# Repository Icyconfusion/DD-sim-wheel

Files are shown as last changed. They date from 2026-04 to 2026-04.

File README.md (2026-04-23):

# DD-sim-wheel
A Direct Drive (DD) wheel for simracing using a hoverboard motor and CAN bus.

I designed this wheel for simracing, to compete with high end direct drive wheels that offer great quality force feedback, except with a much lower price. The wheel has the capability to connect wheel rims, pedals, shifters, handbrakes etc and send those inputs, along with steering position to the PC as game inputs. In creating this project, I learned a lot about motor control and half bridge drivers.


# Assembly

The project can be separated into two parts, the wheelbase and the wheel rim.

For the wheelbase, the assembly consists of four horizontal 2020 profiles, allowing for mounting to rigs etc, and providing the basic structure of the base. Two vertical posts are attached by 90 degree connectors to enable mounting the cross beam for the motor.





The crossbeam (2040 profile) is important as it is the base structure for supporting and holding the motor in place. A thin steel plate (necessary to prevent damage and subsequent twisting of the the crossbeam as a result of the motor axle) is attached to the profile, with the flat part of the motor axle being locked on with the 3d printed clamp. This is the mechanism for holding the motor in place and preventing rotation in the axle. 





To prepare the motor, it is first necessary to disassemble it. First remove the tire as this wont be needed. Then remove the motor bell as we will need to drill holes into it. We will also need to drill into the axle. a 6x70mm bolt pattern is drilled in to the bell face, as well as a 30mm hole in the centre. This allows the mounting of the encoder and routing of wires. Drill a hole in the closed end of the axle, so that wires can run through.



The MT6701 encoder is attached to its mount, then press fit into the bearing on the bell side of the motor.





The diametric magnet for the encoder is glued into the hole on the inside of the magnet mount, this will be attached to the motor along with the quick release using the 6x70mm drilled holes.







The side covers attach to the four horizontal profiles using T nuts, and the PSU is mounted to the side cover using the mounting threads in the psu. The PCB is attached to its mount using the mounting holes, then attached to the vertical profile.











The USB C connectors are screwed onto the back plate, and power cables run through the two holes. The back, top and bottom plates/covers are mounted using T nuts.





The front plate is screwed directly into the tapped ends of the profiles. This is the wheelbase assembly.







For the wheel rim assembly, is is as simple as mounting the 12mm buttons using the nuts included, running the cable from the mcu into the USB c connector in the quick release, and then mounting the wheel rim, buttons box/plates and quick release using screws, and then pushing onto wheelbase.









# Electronics

### Schematic


I made my own 3 phase motor driver to handle the control of the hoverboard motor:


It uses an INA240 for current sensing for torque control, and an IR2104 IC so that the STM32 can control the MOSFETS.



Screw terminals to external connections:


And brake resistor circuit:


### PCB



It has M6 mounting holes for the wheelbase PCB mount. The PCB is organised with the motor driver at the top, and low voltage components below the STM32, which is connected by headers. It uses TO-220 mosfets, and 7.62mm screw terminals. The screw terminals on the bottom are to CAN connections, encoder and 5v power.



# Firmware

The wheelbase uses a modified version of OpenFFBoard firmware. OpenFFboard controls the motor including torque, responding to output from the PC/game to provide force feedback. I added my own CAN firmware into this to recieve CAN messages as inputs, and send them to the PC. This included writing my own CAN callback into the firmware.
For the wheel rim MCU, I wrote my own firmware for reading button inputs, and then sending via CAN bus. The MCU will only send a message when their is a change in button states e.g a press or release, this is to reduce interruption to the motor control firmware. The can message is as follows: if button one is pressed, then 00000001, which is 1x01. Or if buttons 1 and 4 are pressed, 00001001, 0x09.

# BOM

### Parts
| Name | Purpose |  Quantity  | Total cost (USD) | Link | Distributor |
|---|---|----|---|---|---|
| 10 ohm resistor | Resistor for the PCB | 5  | 1.32  | https://www.aliexpress.com/item/1005001437016232.html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 | Aliexpress |
| 90 degree brackets | mounting and assembling T slot profiles | 8  | 0.73  | https://jlcmc.com/product/s/T02/TPDB/die-cast-corner-bracket-eu-20-series-connector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 | JLCMC |
| T nuts | Mounting components to T slot profiles | 60 | 7.23  | https://www.aliexpress.com/item/1005007825040716.html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 | Aliexpress |
| Screws | M5 screws for assembling components. 10 of 16mm, 20 of 14mm, 4 of 30mm, 6 of 45mm, 6 of 65mm, 16 of 8mm. Also 10 of M2x14mm. | 76 | 1.79  | https://jlcmc.com/product/s/E02/EDLA/hex-socket-screw-full-partial-thread-standard-type-(din-912-gb-t-70.1) | JLCMC |
| IR2104 | IC for powering each phases mosfet | 3  | 2.28  | https://www.aliexpress.com/item/1005005970327760.html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 | Aliexpress |
| Small Cap | 0.47 uF 50V CAP | 10 | 5.03  | https://www.aliexpress.com/item/1005009938373275.html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 | Aliexpress |
| LM2596 | Buck converter for supplying low voltage power to the PCB | 1  | 2.56  | https://www.aliexpress.com/item/1005010036505161.html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 | Aliexpress |
| INA240 | The current amplifier to sense motor current with the shunt | 3  | 11.48 | https://www.aliexpress.com/item/1005007050377087.html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 | Aliexpress |
| MOSFET | IRF2204 mosfet for the 3 phase motor driver | 3  | 5.63  | https://www.aliexpress.com/item/1005008398718849.html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 | Aliexpress |
| Large Cap | 50V 2200uF capacitor for smoothing across power lines | 1  | 12.76 | https://www.aliexpress.com/item/1005005380342459.html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 | Aliexpress |
| MT6701 | The MT6701 is the encoder to track the position of the wheel rim. | 1  | 3.27  | https://www.aliexpress.com/item/1005010143099990.html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 | Aliexpress |
| STM32 | STM32 is the wheelbase PCB MCU. It runs the FFB firmware. | 1  | 10.62 | https://www.aliexpress.com/item/1005009620785965.html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 | Aliexpress |
| TVS diode | P6KE36A TVS diode for power on the PCB | 1  | 2.66  | https://www.aliexpress.com/item/1005008668996384.html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 | Aliexpress |
| RP2350 | RP2350 CAN is the devboard for the wheel rim. It has CAN included. | 1  | 16.93 | https://www.aliexpress.com/item/1005008827015596.html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 | Aliexpress |
| CAN resistor | 120 ohm termination resistor for CAN bus. | 2  | 1.35  | https://www.aliexpress.com/item/1005006730653425.html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 | Aliexpress |
| Shunt resistor | Constantan wire resistor for motor current sensing. 10mr 1.5x20 | 3  | 1.63  | https://www.aliexpress.com/item/1005003122854809.html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 | Aliexpress |
| Push Buttons | The pushbuttons are used for the steering rim as the controls. | 8  | 1.54  | https://www.aliexpress.com/item/1005006341090307.html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 | Aliexpress |
| CAN transciever | SN65HVD230 Can transceiver for communicating between wheelbase and wheel rim | 1  | 3.93  | https://www.aliexpress.com/item/1005006693506982.html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 | Aliexpress |
| Brake resistor | 500W 3.3R brake resistor for motor control | 1  | 20.19 | https://www.aliexpress.com/item/1005002672337729.html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 | Aliexpress |
| Steering wheel | The steering wheel rim | 1  | 23.10 | https://www.aliexpress.com/item/1005008283871869.html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 | Aliexpress |
| Quick release | Quick release for mechanically attaching the rim to the wheelbase | 1  | 30.44 | https://www.aliexpress.com/item/1005006011448738.html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 | Aliexpress |
| USB C male connector | For use in the steering rim to connect it and transfer data/power to and from the wheelbase | 1  | 3.51  | https://www.aliexpress.com/item/1005009243305185.html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 | Aliexpress |
| USB C female connector | For connecting pedals, handbrake etc to the wheelbase. They are also used for connecting the rim. | 5  | 2.04  | https://www.aliexpress.com/item/1005008529430881.html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 | Aliexpress |
| PSU | 36v 800w psu for driving the motor and electronics | 1  | 27.31 | https://www.aliexpress.com/item/1005010376385581.html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 | Alixpress  |
| Hoverboard motor | 36v 350w hoverboard motor to provide the force feedback. | 1  | 32.22 | https://www.aliexpress.com/item/1005009897349541.html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 | Aliexpress |
| Steel plate | For clamping the motor shaft and protecting the aluminium crossbeam. 3mm thick. | 1  | 9.29  | https://www.aliexpress.com/item/1005007253220639.html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 | Aliexpress |
| 2040 T slot 180mm | The crossbeam for supporting the motor shaft. | 1  | 0.80  | https://jlcmc.com/product/s/T01/TXCJ/extruded-aluminum-t-slot-20-series(eu) | JLCMC |
| T slot 200mm | The vertical supports for 2060, PCB and PSU | 2  | 1.05  | https://jlcmc.com/product/s/T01/TXCJ/extruded-aluminum-t-slot-20-series(eu) | JLCMC |
| T slot 320mm | Providing the outer horizontal frame | 4  | 3.28  | https://jlcmc.com/product/s/T01/TXCJ/extruded-aluminum-t-slot-20-series(eu) | JLCMC |

### Printed parts

| Name| Quantity|Picture|
|---|---|---|
|Side cover| 1|
|PSU side cover| 1|
|Top plate | 1|
|Top cover| 1|
|Bottom cover| 1|
|Back cover| 1|
|Front cover| 1|
|Axle clamp| 1|
|Encoder module| 1|
|Magnet module| 1|
|PCB mount| 1|
|Wheel button plate| 1|

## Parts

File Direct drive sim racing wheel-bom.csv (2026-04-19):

Name | Purpose | Quantity | Total Cost (USD) | Link | Distributor
PCB | PCB for all the components | 1 | 13.58 | https://cart.jlcpcb.com/quote?stencilLayer=2&stencilWidth=100&stencilLength=100&stencilCounts=5&plateType=1 | JLCPCB
10 ohm resistor | Resistor for the PCB | 5 | 1.32 | https://www.aliexpress.com/item/1005001437016232.html?curPageLogUid=U5uodymgkUGQ | Aliexpress
90 degree brackets | mounting and assembling T slot profiles | 8 | 0.73 | https://jlcmc.com/product/s/T02/TPDB/die-cast-corner-bracket-eu-20-series-connector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 | JLCMC
T nuts | Mounting components to T slot profiles | 60 | 7.23 | https://www.aliexpress.com/item/1005007825040716.html?curPageLogUid=qxyuanETgGiG | Aliexpress
Screws | M5 screws for assembling components. 10 of 16mm, 20 of 14mm, 4 of 30mm, 6 of 45mm, 6 of 65mm, 16 of 8mm. Also 10 of M2x14mm. | 76 | 1.79 | https://jlcmc.com/product/s/E02/EDLA/hex-socket-screw-full-partial-thread-standard-type-(din-912-gb-t-70.1) | JLCMC
IR2104 | IC for powering each phases mosfet | 3 | 2.28 | https://www.aliexpress.com/item/1005005970327760.html?curPageLogUid=UiB2F2SOtrNB | Aliexpress
Small Cap | 0.47 uF 50V CAP | 10 | 5.03 | https://www.aliexpress.com/item/1005009938373275.html?curPageLogUid=g6TO5H8pSlm0 | Aliexpress
LM2596 | Buck converter for supplying low voltage power to the PCB | 1 | 2.56 | https://www.aliexpress.com/item/1005010036505161.html?curPageLogUid=02yFEsARBKx0 | Aliexpress
INA240 | The current amplifier to sense motor current with the shunt | 3 | 11.48 | https://www.aliexpress.com/item/1005007050377087.html?curPageLogUid=PooybKR7LpTQ | Aliexpress
MOSFET | IRF2204 mosfet for the 3 phase motor driver | 3 | 5.63 | https://www.aliexpress.com/item/1005008398718849.html?curPageLogUid=EANWfiNw3IgJ | Aliexpress
Large Cap | 50V 2200uF capacitor for smoothing across power lines | 1 | 12.76 | https://www.aliexpress.com/item/1005005380342459.html?curPageLogUid=RPVryHdchNX4 | Aliexpress
MT6701 | The MT6701 is the encoder to track the position of the wheel rim. | 1 | 3.27 | https://www.aliexpress.com/item/1005010143099990.html?curPageLogUid=xzfgW3svUKzg | Aliexpress
STM32 | STM32 is the wheelbase PCB MCU. It runs the FFB firmware. | 1 | 10.62 | https://www.aliexpress.com/item/1005009620785965.html?curPageLogUid=iACQ9ztcidY0 | Aliexpress
TVS diode | P6KE36A TVS diode for power on the PCB | 1 | 2.66 | https://www.aliexpress.com/item/1005008668996384.html?curPageLogUid=yzE7XJPgJBo8 | Aliexpress
RP2350 | RP2350 CAN is the devboard for the wheel rim. It has CAN included. | 1 | 16.93 | https://www.aliexpress.com/item/1005008827015596.html?curPageLogUid=vOb7IYHAYoA1 | Aliexpress
CAN resistor | 120 ohm termination resistor for CAN bus. | 2 | 1.35 | https://www.aliexpress.com/item/1005006730653425.html?curPageLogUid=c0lLXeUYCSua | Aliexpress
Shunt resistor | Constantan wire resistor for motor current sensing. 10mr 1.5x20 | 3 | 1.63 | https://www.aliexpress.com/item/1005003122854809.html?curPageLogUid=jjHaL1Mq2xuj | Aliexpress
Push Buttons | The pushbuttons are used for the steering rim as the controls. | 8 | 1.54 | https://www.aliexpress.com/item/1005006341090307.html?curPageLogUid=qpi8KIvDRT09 | Aliexpress
CAN transciever | SN65HVD230 Can transceiver for communicating between wheelbase and wheel rim | 1 | 3.93 | https://www.aliexpress.com/item/1005006693506982.html?curPageLogUid=lR7HKQJall19 | Aliexpress
Brake resistor | 500W 3.3R brake resistor for motor control | 1 | 20.19 | https://www.aliexpress.com/item/1005002672337729.html?curPageLogUid=hIX4clt2NvSe | Aliexpress
Steering wheel | The steering wheel rim | 1 | 23.10 | https://www.aliexpress.com/item/1005008283871869.html?curPageLogUid=euxCJDX6zvuV | Aliexpress
Quick release | Quick release for mechanically attaching the rim to the wheelbase | 1 | 30.44 | https://www.aliexpress.com/item/1005006011448738.html?curPageLogUid=kRrVs4aPaLjf | Aliexpress
USB C male connector | For use in the steering rim to connect it and transfer data/power to and from the wheelbase | 1 | 3.51 | https://www.aliexpress.com/item/1005009243305185.html?curPageLogUid=0OJ39zZ4TCBB | Aliexpress
USB C female connector | For connecting pedals, handbrake etc to the wheelbase. They are also used for connecting the rim. | 5 | 2.04 | https://www.aliexpress.com/item/1005008529430881.html?curPageLogUid=Uu7WJVr0K4pu | Aliexpress
PSU | 36v 800w psu for driving the motor and electronics | 1 | 27.31 | https://www.aliexpress.com/item/1005010376385581.html?curPageLogUid=77qK0odrpWPv | Alixpress
Hoverboard motor | 36v 350w hoverboard motor to provide the force feedback. | 1 | 32.22 | https://www.aliexpress.com/item/1005009897349541.html?curPageLogUid=29wSyuul6Ael | Aliexpress
Steel plate | For clamping the motor shaft and protecting the aluminium crossbeam. 3mm thick. | 1 | 9.29 | https://www.aliexpress.com/item/1005007253220639.html?curPageLogUid=3KQb5Kkc63sV | Aliexpress
2040 T slot 180mm | The crossbeam for supporting the motor shaft. | 1 | 0.80 | https://jlcmc.com/product/s/T01/TXCJ/extruded-aluminum-t-slot-20-series(eu) | JLCMC
T slot 200mm | The vertical supports for 2060, PCB and PSU | 2 | 1.05 | https://jlcmc.com/product/s/T01/TXCJ/extruded-aluminum-t-slot-20-series(eu) | JLCMC
T slot 320mm | Providing the outer horizontal frame | 4 | 3.28 | https://jlcmc.com/product/s/T01/TXCJ/extruded-aluminum-t-slot-20-series(eu) | JLCMC

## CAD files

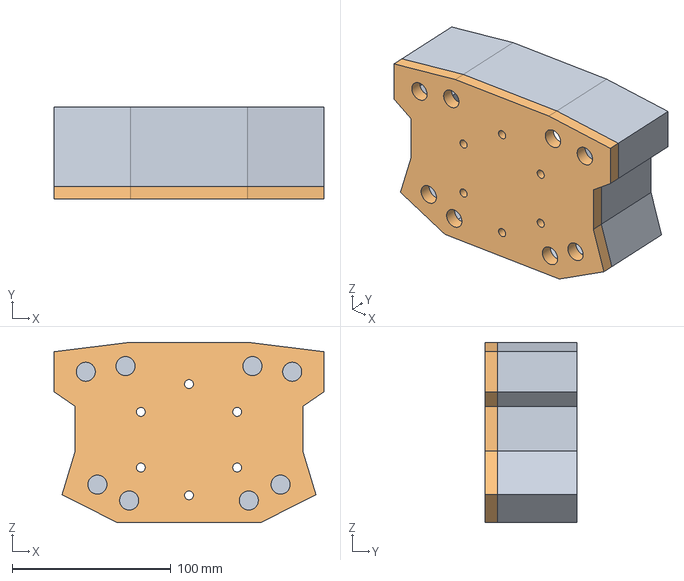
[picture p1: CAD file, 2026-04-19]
CAD/Wheel button plate.step
169.9 x 58.0 x 113.5 mm

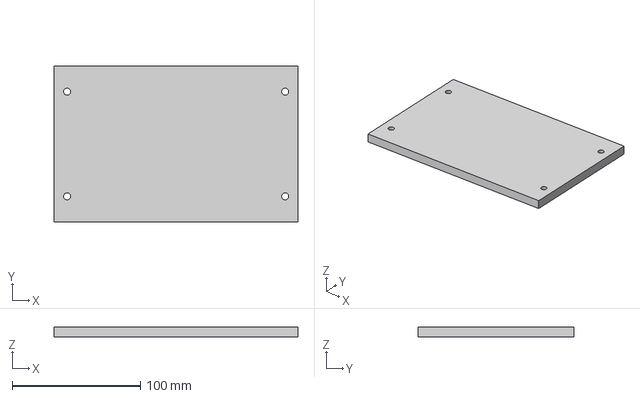
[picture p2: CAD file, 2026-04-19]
CAD/Top plate.step
190.3 x 121.6 x 8.00 mm

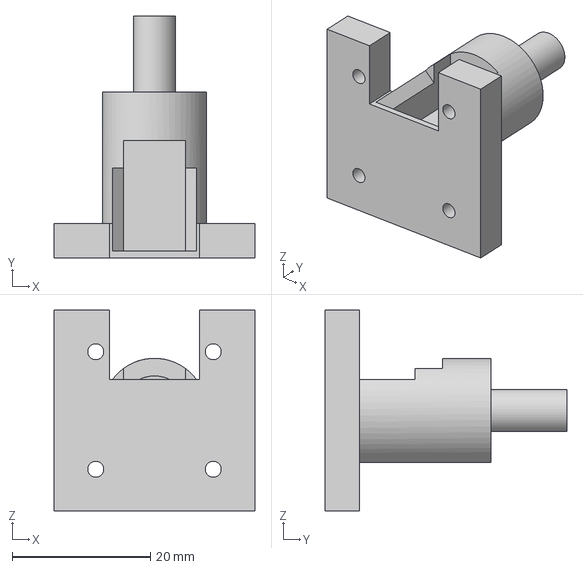
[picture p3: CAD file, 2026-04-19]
CAD/Encoder module.step
29.0 x 35.0 x 29.0 mm

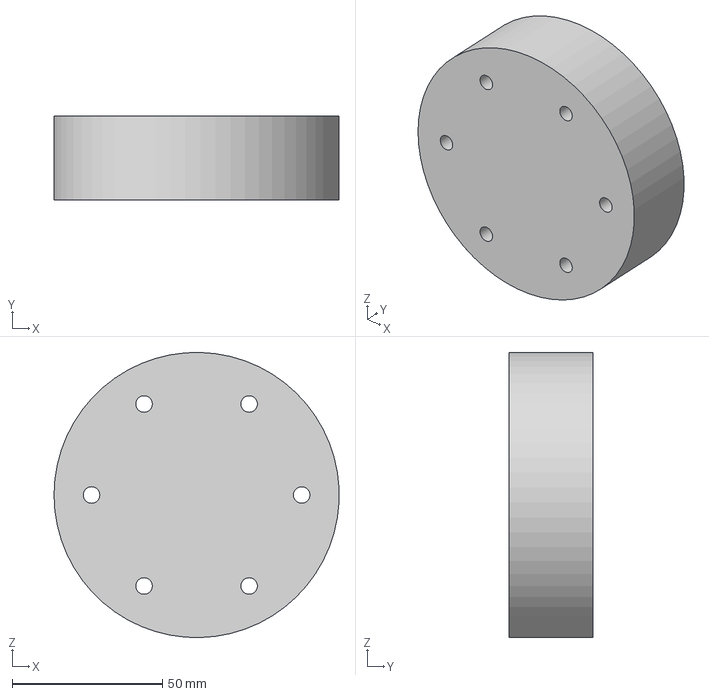
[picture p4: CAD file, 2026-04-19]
CAD/Magnet module.step
94.9 x 28.0 x 95.0 mm

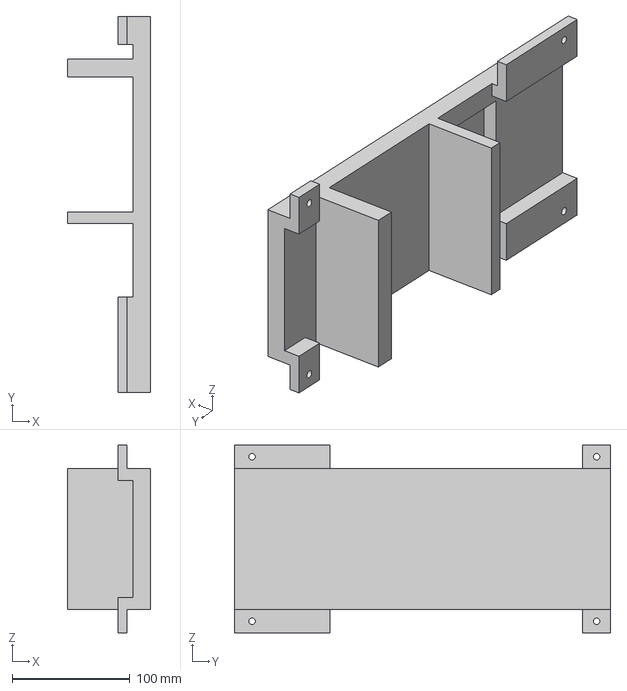
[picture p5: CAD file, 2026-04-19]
CAD/side cover psu side.step
71.0 x 320.1 x 160.0 mm

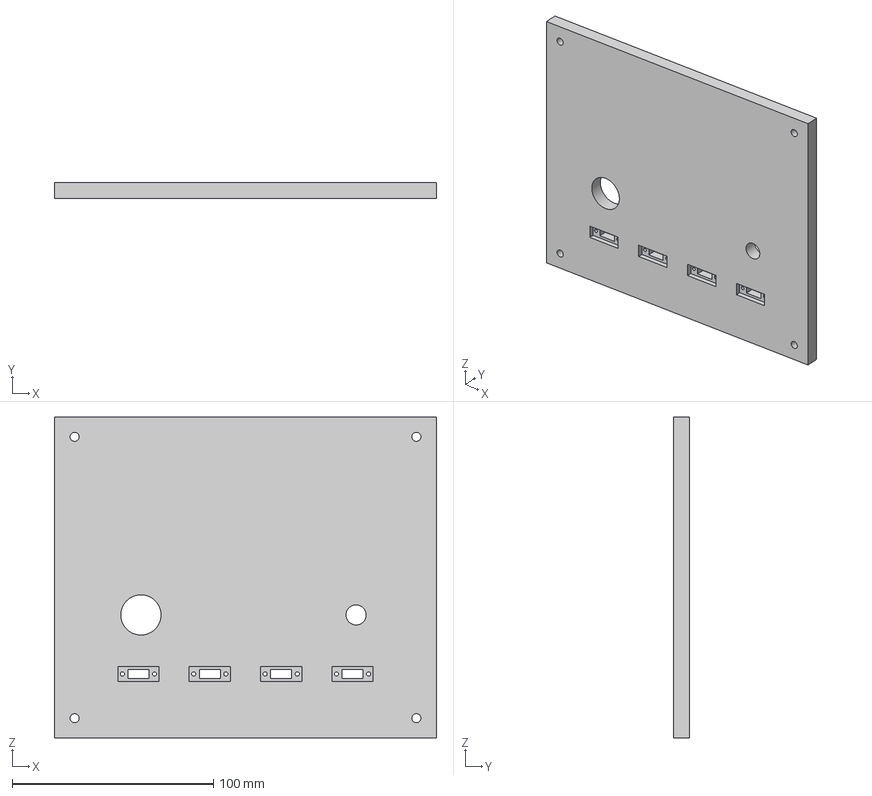
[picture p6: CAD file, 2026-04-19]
CAD/Back plate.step
190.0 x 8.00 x 159.5 mm

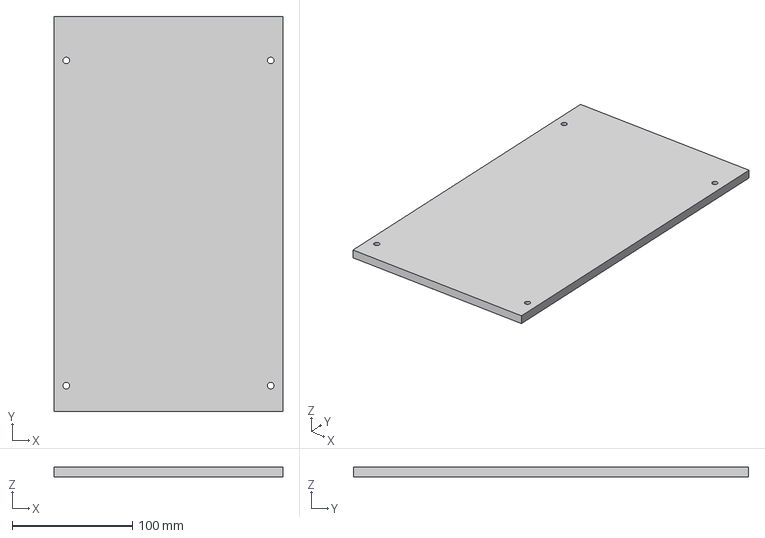
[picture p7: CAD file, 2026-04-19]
CAD/bottom plate.step
190.0 x 328.4 x 8.00 mm

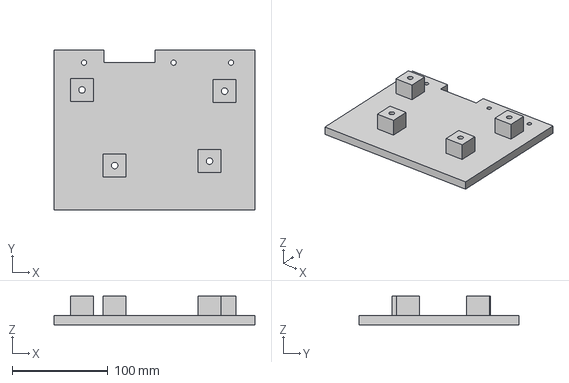
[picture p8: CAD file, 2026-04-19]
CAD/PCB mount.step
210.0 x 167.3 x 30.0 mm

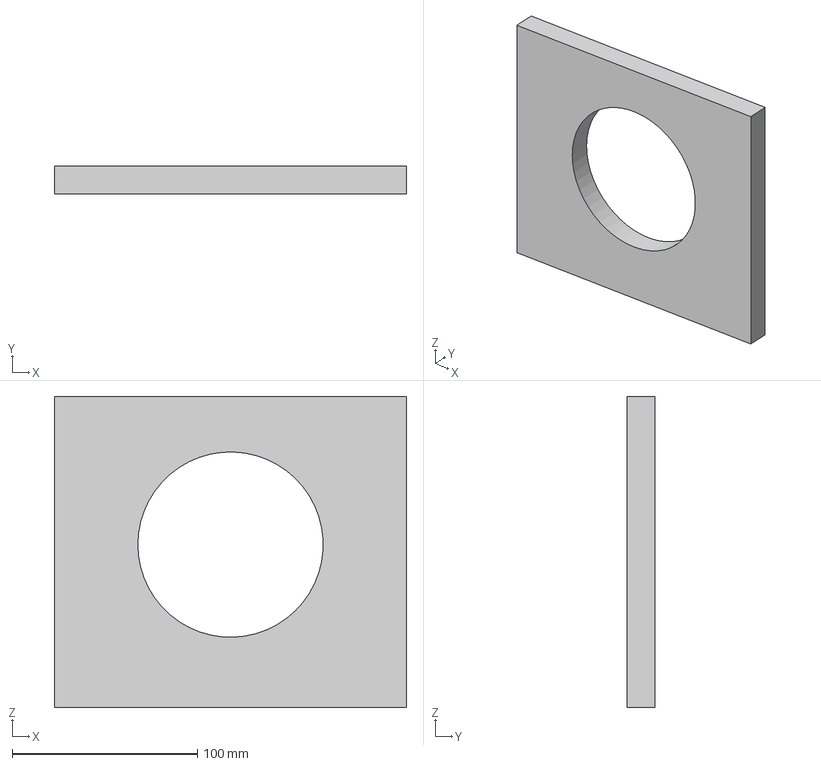
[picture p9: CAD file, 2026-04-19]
CAD/Front cover.step
190.0 x 15.0 x 168.0 mm

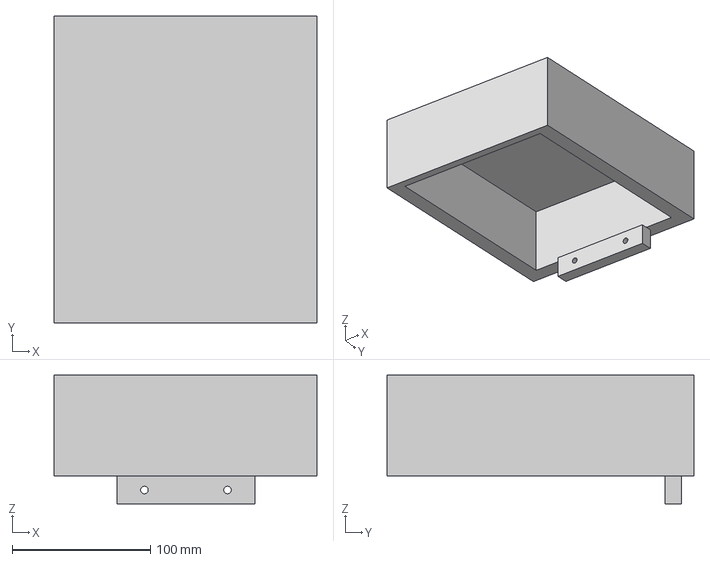
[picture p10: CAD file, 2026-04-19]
CAD/Top cover.step
190.0 x 221.8 x 93.0 mm

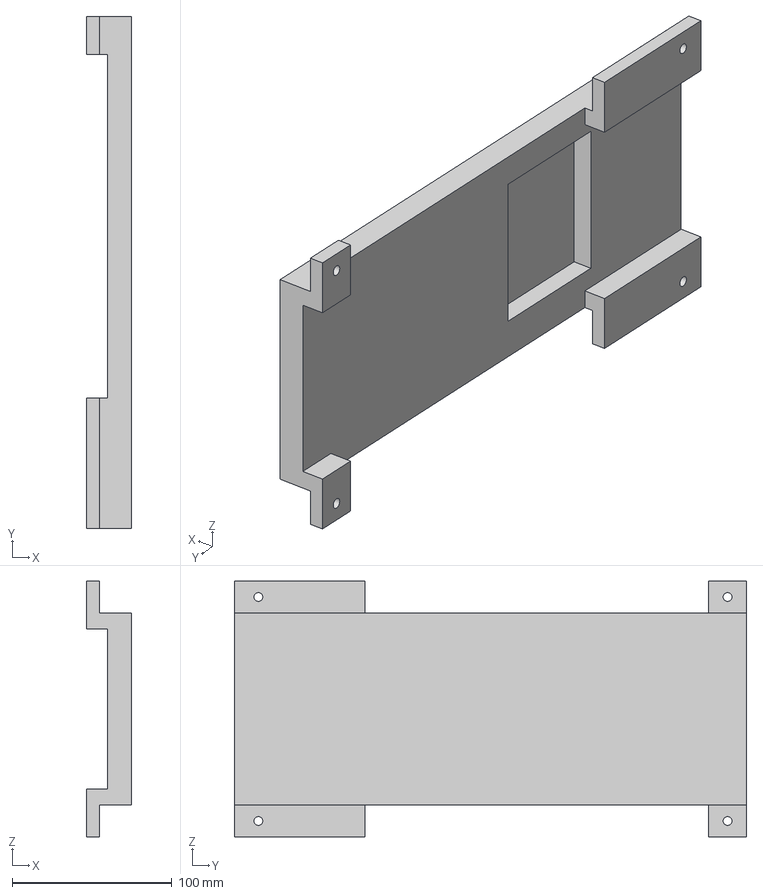
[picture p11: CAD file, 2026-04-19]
CAD/side cover.step
28.0 x 320.1 x 160.0 mm

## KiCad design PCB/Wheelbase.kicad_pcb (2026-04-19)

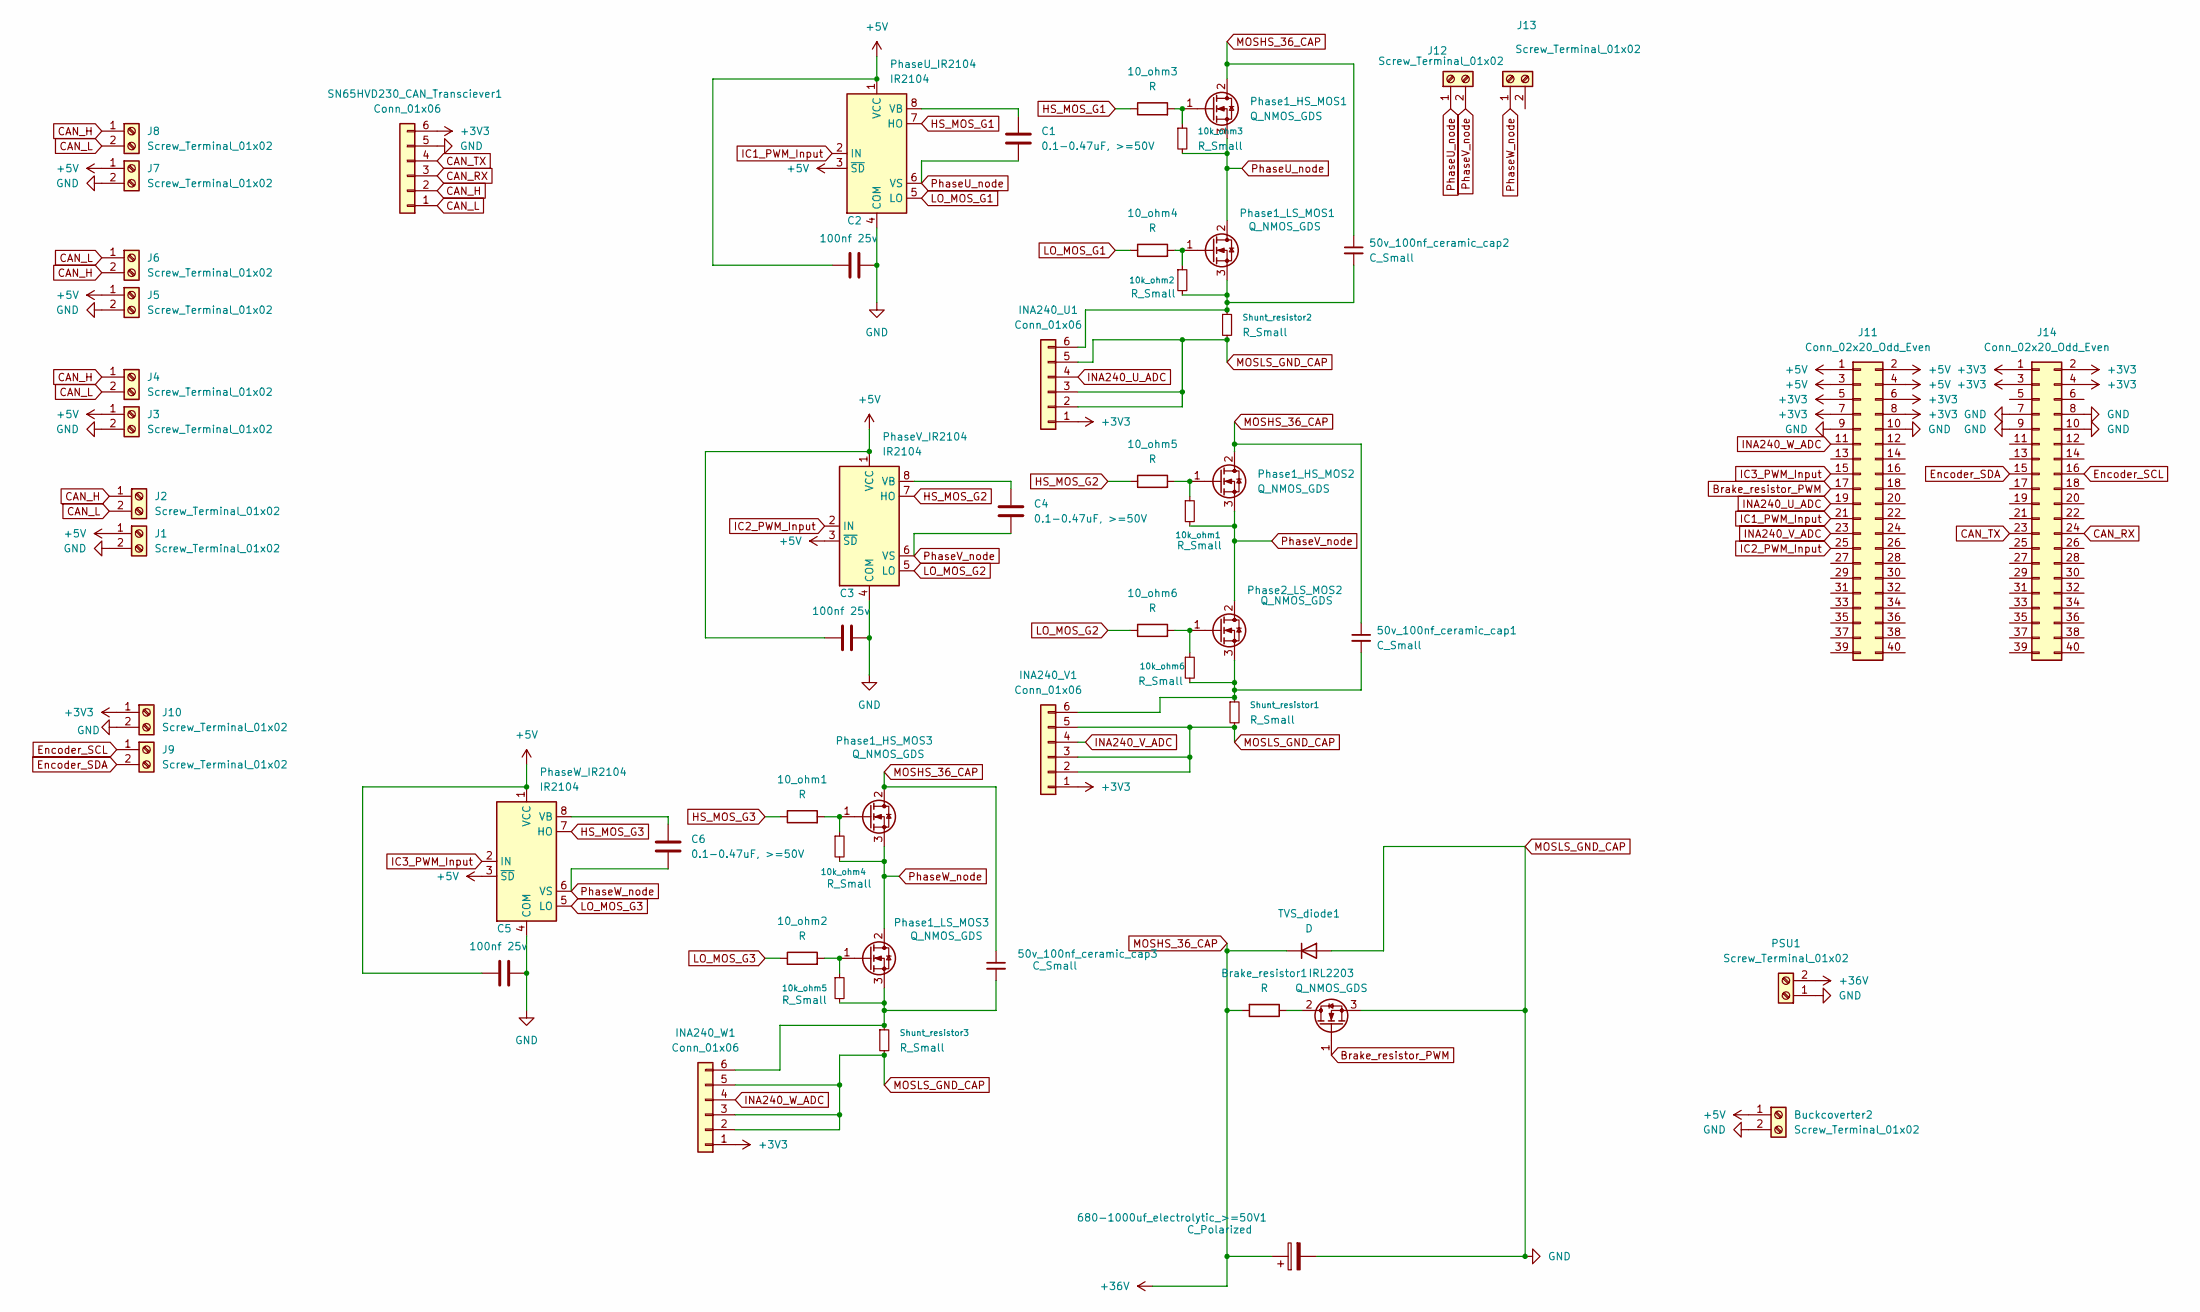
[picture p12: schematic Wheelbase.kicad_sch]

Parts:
10_ohm1, 10_ohm2, 10_ohm3, 10_ohm4, 10_ohm5, 10_ohm6: R; R_Axial_DIN0207_L6.3mm_D2.5mm_P5.08mm_Vertical
10k_ohm1, 10k_ohm2, 10k_ohm3, 10k_ohm4, 10k_ohm5, 10k_ohm6: R_Small; R_Axial_DIN0207_L6.3mm_D2.5mm_P5.08mm_Vertical
50v_100nf_ceramic_cap1, 50v_100nf_ceramic_cap2, 50v_100nf_ceramic_cap3: C_Small; C_Disc_D7.5mm_W5.0mm_P7.50mm
680-1000uf_electrolytic_>=50V1: C_Polarized; CP_Radial_D12.5mm_P2.50mm
Brake_resistor1: R; Wuerth_691311400102_P7.62mm
Buckcoverter2: Screw_Terminal_01x02; Wuerth_691311400102_P7.62mm
C1, C4, C6: 0.1-0.47uF, >=50V; CP_Radial_D5.0mm_P2.50mm
C2, C3, C5: 100nf 25v; C_Disc_D5.0mm_W2.5mm_P2.50mm
INA240_U1, INA240_V1, INA240_W1: Conn_01x06; PinHeader_1x06_P2.54mm_Vertical
IRL2203: Q_NMOS_GDS; TO-220-3_Vertical
J1, J2, J3, J4, J5, J6, J7, J8, J9, J10, J12, J13: Screw_Terminal_01x02; Wuerth_691311400102_P7.62mm
J11, J14: Conn_02x20_Odd_Even; PinHeader_2x20_P2.54mm_Vertical
PSU1: Screw_Terminal_01x02; Wuerth_691311400102_P7.62mm
Phase1_HS_MOS1, Phase1_HS_MOS2, Phase1_HS_MOS3, Phase1_LS_MOS1, Phase1_LS_MOS3, Phase2_LS_MOS2: Q_NMOS_GDS; TO-220-3_Vertical
PhaseU_IR2104: IR2104; DIP-8_W7.62mm
PhaseV_IR2104: IR2104; DIP-8_W7.62mm
PhaseW_IR2104: IR2104; DIP-8_W7.62mm
SN65HVD230_CAN_Transciever1: Conn_01x06; PinHeader_1x06_P2.54mm_Vertical
Shunt_resistor1, Shunt_resistor2, Shunt_resistor3: R_Small; R_Axial_Power_L20.0mm_W6.4mm_P22.40mm
TVS_diode1: D; D_T-1_P5.08mm_Horizontal

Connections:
+3V3: INA240_U1.1, INA240_V1.1, INA240_W1.1, J10.1, J11.5, J11.6, J11.7, J11.8, J14.1, J14.2, J14.3, J14.4, SN65HVD230_CAN_Transciever1.6
+5V: Buckcoverter2.1, C2.1, C3.1, C5.1, J1.1, J3.1, J5.1, J7.1, J11.1, J11.2, J11.3, J11.4, PhaseU_IR2104.1 (VCC), PhaseU_IR2104.3 (~SD), PhaseV_IR2104.1 (VCC), PhaseV_IR2104.3 (~SD), PhaseW_IR2104.1 (VCC), PhaseW_IR2104.3 (~SD)
Brake_resistor_PWM: IRL2203.1 (G), J11.17
CAN_H: J2.1, J4.1, J6.2, J8.1, SN65HVD230_CAN_Transciever1.2
CAN_L: J2.2, J4.2, J6.1, J8.2, SN65HVD230_CAN_Transciever1.1
CAN_RX: J14.24, SN65HVD230_CAN_Transciever1.3
CAN_TX: J14.23, SN65HVD230_CAN_Transciever1.4
Encoder_SCL: J9.1, J14.16
Encoder_SDA: J9.2, J14.15
HS_MOS_G1: 10_ohm3.1, PhaseU_IR2104.7 (HO)
HS_MOS_G2: 10_ohm5.1, PhaseV_IR2104.7 (HO)
HS_MOS_G3: 10_ohm1.1, PhaseW_IR2104.7 (HO)
IC1_PWM_Input: J11.21, PhaseU_IR2104.2 (IN)
IC2_PWM_Input: J11.25, PhaseV_IR2104.2 (IN)
IC3_PWM_Input: J11.15, PhaseW_IR2104.2 (IN)
INA240_U_ADC: INA240_U1.4, J11.19
INA240_V_ADC: INA240_V1.4, J11.23
INA240_W_ADC: INA240_W1.4, J11.11
LO_MOS_G1: 10_ohm4.1, PhaseU_IR2104.5 (LO)
LO_MOS_G2: 10_ohm6.1, PhaseV_IR2104.5 (LO)
LO_MOS_G3: 10_ohm2.1, PhaseW_IR2104.5 (LO)
MOSHS_36_CAP: 50v_100nf_ceramic_cap1.1, 50v_100nf_ceramic_cap2.1, 50v_100nf_ceramic_cap3.1, 680-1000uf_electrolytic_>=50V1.1, Brake_resistor1.2, PSU1.2, Phase1_HS_MOS1.2 (D), Phase1_HS_MOS2.2 (D), Phase1_HS_MOS3.2 (D), TVS_diode1.1 (K); also elsewhere on the board
MOSLS_GND_CAP: 680-1000uf_electrolytic_>=50V1.2, Buckcoverter2.2, C2.2, C3.2, C5.2, INA240_U1.2, INA240_U1.3, INA240_U1.5, INA240_V1.2, INA240_V1.3, INA240_V1.5, INA240_W1.2, INA240_W1.3, INA240_W1.5, IRL2203.3 (S), J1.2, J3.2, J5.2, J7.2, J10.2, J11.9, J11.10, J14.7, J14.8, J14.9, J14.10, PSU1.1, PhaseU_IR2104.4 (COM), PhaseV_IR2104.4 (COM), PhaseW_IR2104.4 (COM), SN65HVD230_CAN_Transciever1.5, Shunt_resistor1.2, Shunt_resistor2.2, Shunt_resistor3.2, TVS_diode1.2 (A)
unnamed 23: 10k_ohm2.2, 50v_100nf_ceramic_cap2.2, INA240_U1.6, Phase1_LS_MOS1.3 (S), Shunt_resistor2.1; also elsewhere on the board
unnamed 24: 10k_ohm6.2, 50v_100nf_ceramic_cap1.2, INA240_V1.6, Phase2_LS_MOS2.3 (S), Shunt_resistor1.1; also elsewhere on the board
unnamed 25: 10k_ohm5.2, 50v_100nf_ceramic_cap3.2, INA240_W1.6, Phase1_LS_MOS3.3 (S), Shunt_resistor3.1; also elsewhere on the board
unnamed: Brake_resistor1.1, IRL2203.2 (D)
unnamed: 10_ohm3.2, 10k_ohm3.1, Phase1_HS_MOS1.1 (G)
unnamed: 10_ohm5.2, 10k_ohm1.1, Phase1_HS_MOS2.1 (G)
unnamed: 10_ohm1.2, 10k_ohm4.1, Phase1_HS_MOS3.1 (G)
unnamed: 10_ohm4.2, 10k_ohm2.1, Phase1_LS_MOS1.1 (G)
unnamed: 10_ohm2.2, 10k_ohm5.1, Phase1_LS_MOS3.1 (G)
unnamed: 10_ohm6.2, 10k_ohm6.1, Phase2_LS_MOS2.1 (G)
unnamed: C1.1, PhaseU_IR2104.8 (VB)
unnamed: C4.1, PhaseV_IR2104.8 (VB)
unnamed: C6.1, PhaseW_IR2104.8 (VB)
PhaseU_node: 10k_ohm3.2, C1.2, J12.1, Phase1_HS_MOS1.3 (S), Phase1_LS_MOS1.2 (D), PhaseU_IR2104.6 (VS)
PhaseV_node: 10k_ohm1.2, C4.2, J12.2, Phase1_HS_MOS2.3 (S), Phase2_LS_MOS2.2 (D), PhaseV_IR2104.6 (VS)
PhaseW_node: 10k_ohm4.2, C6.2, J13.1, Phase1_HS_MOS3.3 (S), Phase1_LS_MOS3.2 (D), PhaseW_IR2104.6 (VS)

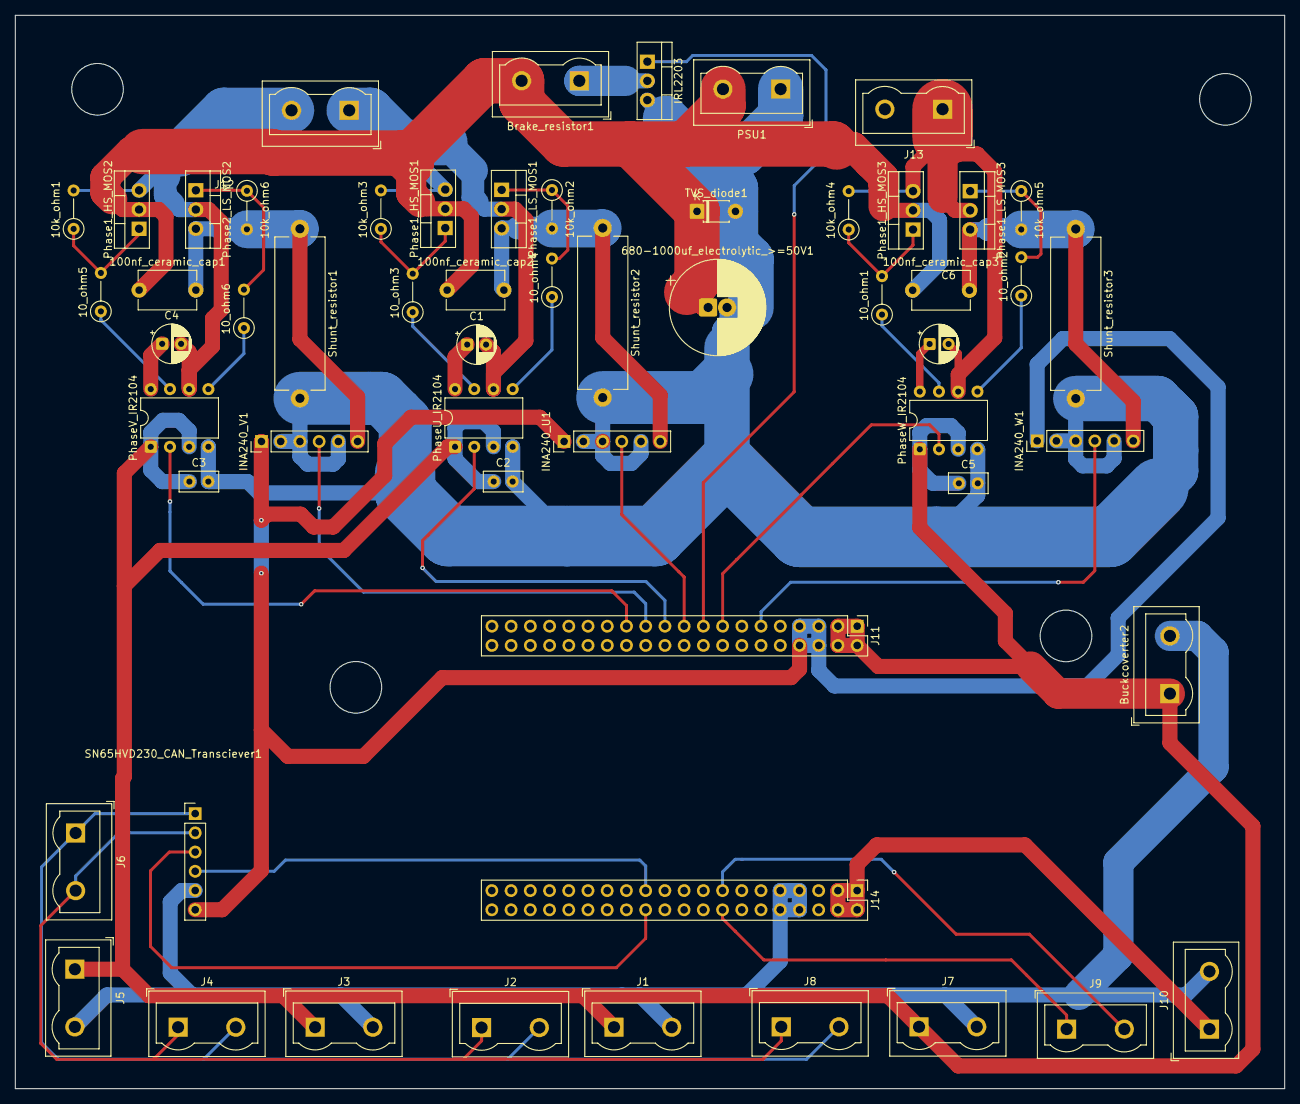
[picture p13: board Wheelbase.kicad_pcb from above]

Board: 2 copper layers, 167.7 x 141.8 mm, 57 parts (0 on the bottom side), 39 nets.

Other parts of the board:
100nf_ceramic_cap1, 100nf_ceramic_cap2, 100nf_ceramic_cap3: C_Small; C_Disc_D7.5mm_W5.0mm_P7.50mm

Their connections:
MOSHS_36_CAP: 100nf_ceramic_cap1.1, 100nf_ceramic_cap2.1, 100nf_ceramic_cap3.1; also elsewhere on the board
unnamed 23: 100nf_ceramic_cap2.2; also elsewhere on the board
unnamed 24: 100nf_ceramic_cap1.2; also elsewhere on the board
unnamed 25: 100nf_ceramic_cap3.2; also elsewhere on the board

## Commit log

2026-04-19 Rename Encoder module.step to CAD/Encoder module.step
    [Encoder module.step]
2026-04-19 Rename Front cover.step to CAD/Front cover.step
    [Front cover.step]
2026-04-19 Rename Magnet module.step to CAD/Magnet module.step
    [Magnet module.step]
2026-04-19 Rename PCB mount.step to CAD/PCB mount.step
    [PCB mount.step]
2026-04-19 Rename Top cover.step to CAD/Top cover.step
    [Top cover.step]
2026-04-19 Rename Top plate.step to CAD/Top plate.step
    [Top plate.step]
2026-04-19 Rename Wheel button plate.step to CAD/Wheel button plate.step
    [Wheel button plate.step]
2026-04-19 Rename bottom plate.step to CAD/bottom plate.step
    [bottom plate.step]
2026-04-19 Rename side cover psu side.step to CAD/side cover psu side.step
    [side cover psu side.step]
2026-04-19 Rename side cover.step to CAD/side cover.step
    [side cover.step]
2026-04-19 Rename Back plate.step to CAD/Back plate.step
    [Back plate.step]
